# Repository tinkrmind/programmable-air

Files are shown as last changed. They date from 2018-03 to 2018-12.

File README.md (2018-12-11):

## NOTE: Development of Programmable-Air has moved to [Programmable-Air Org repo](https://github.com/programmable-air). This repo is maintained for the sake of completeness but is no longer actively maintained. Please use [Programmable-Air Org repo](https://github.com/programmable-air) for code and reference material.

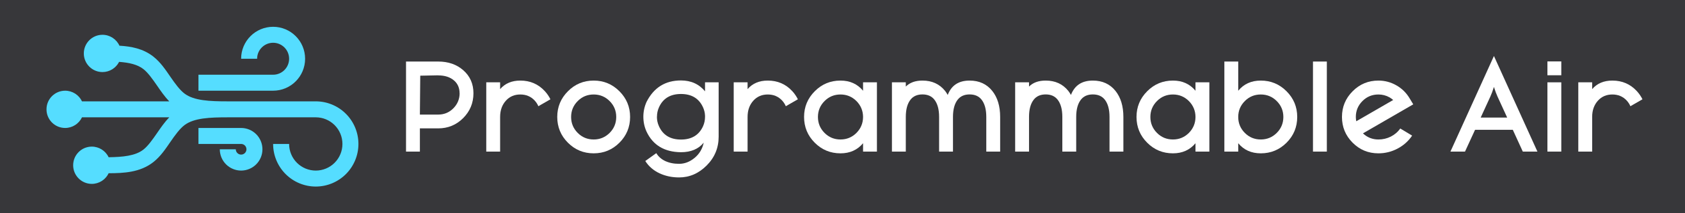
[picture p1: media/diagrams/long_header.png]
Header


## Buzz

* [Hackaday mention!](https://hackaday.com/2018/05/24/programmable-air-makes-robotics-a-breeze/)
* [Hackster mention!!](https://blog.hackster.io/programmable-air-is-an-arduino-based-air-pump-for-your-soft-robotics-projects-9945c6ed96aa)
* [Maker Faire](https://makerfaire.com/maker/entry/67747/)

## Elevator Pitch

quad-chart (https://docs.google.com/presentation/d/1pUnGk4v_wuCpisjBpNWZSJUyDwAFb4v1xceV4rX-Uv4/edit?usp=sharing)

### [Slideshow](https://docs.google.com/presentation/d/1pUnGk4v_wuCpisjBpNWZSJUyDwAFb4v1xceV4rX-Uv4/edit?usp=sharing)

I started out making in earnest at IISc where I saw researchers being exploited by hardware manufacturers. Sub-par equipment is often lauded as the best solution only because it's the only solution. As a result I worked directly with researchers making equipment for measuring elephant height, insect wing- beat frequency, underwater gates for fishes.. I see the same issue with soft robotics today.

The field of inflatable robotics is still in its infancy. So there are a lot of low hanging fruit up for grabs. As such, the more people involved in active experimentation, the faster the field will mature.

Working with inflatables involves a lot of prototyping as a part of the design process. To do any repeatable experiments with inflatables, a controllable air source is required.

I feel there isn't any affordable and easy to use programmable air source available for makers right now. This is a barrier to entry. Programmable Air is my attempt to create a bottom of the line air source that is cheaper and easier to use than anything available right now. The market is strapped for cash makers and schools.

### What can you use it for?

#### Vacuum

###### [* Electronic component pick and place.](https://vimeo.com/268358924)

SMD component pick and place (https://vimeo.com/268358924)

###### [* Universal vacuum based gripper.](https://vimeo.com/268358891)

Universal vacuum based gripper (https://vimeo.com/268358891)

#### Inflatable

###### [* Crazy soft robots]()

###### [* Balloons!](https://vimeo.com/268358970)

Balloons! (https://vimeo.com/268358970)

##### [* Small air brush?](https://vimeo.com/268163619)

Doesn't really work. You can get it to work if the air brush is pointing down and mars is on retrograde :P Check out the failed video below. Maybe it'll give you an idea for how you can improve on it.

Air-Brush (https://vimeo.com/268163619)

 Most airbrushes seem to require around 10L/min air flow rate and the current pump can only deliver 1-2L/min. This small one just barely works with the pumps.

#### Pressure sensor

##### [* Large Impact Sensors]((https://vimeo.com/268358944)

Irregular impact sensors (https://vimeo.com/268358944)

Any closed inflated object can be used as an impact sensor when connected to the air pressure sensor e.g. a large flexible tube with one end closed off and another connected to the pressure sensor. When the tube is pressed a pressure spike is recorded by the sensor. This tube can be looped around a bumper car for example to act as an impact sensor.

##### [Exhalation](https://vimeo.com/268359027)

Exhalation (https://vimeo.com/268359027)

Controlling the air pressure inside a closed chamber allows a soft robot place in the chamber to behave as if it is being controlled without any tubes connected to  it. This facilitates easy prototyping and some funky art pieces. Inspired from [Exhalation](http://escapepod.org/2009/04/10/ep194-exhalation/) by Ted Chiang.

### What's wrong with the current solutions?

#### Pneuduino: [link](http://pneuduino.org/)

Not available for purchase. Potentially fallen out of development(last commit on github was about two years and the primary engineer has graduated out of the program.)

#### Fluidic control system: [link](https://softroboticstoolkit.com/book/control-board)

Truly designed by researchers for reserchers. Ugly. Complicated to setup. Needlessly expensive. [BOM](https://softroboticstoolkit.com/book/controlboard-bom)

Methods of potentially reducing cost:

- __Cheaper pump__: The [current pump](http://ph.parker.com/us/12051/en/btc-iis-and-ttc-iis-miniature-diaphragm-pump) at ~288$ is overpriced if not necessarily overspec'ed. I'm confident a replacement would be available for one tenth the cost.
- __Cheaper valves__: High switching rate is not necessary for most applications. The current valves cost ~175$. An acceptable replacement would be [this](https://www.elecrow.com/dc12v-four-way-valve-independent-control-solenoid-valve.html) at ~10$. Since pressure is controlled by PWM of the valves, this may lead to some issues if these actuators can't be driven fast enough. Some slack can be made up for by adding a "capacitor" after the valve. But, if the actuation time is of the order of hundreds of milliseconds, I may need a different approach. One such approach can be servo driven drip knobs. Another approach could be a linear actuator driving a plate covering a slit
- __Get rid of the power boards__: There's no need for a 24V in which then gets converted to 12V and 5V on board. It adds bulk and points of failure. Separate 12V and 5V wall warts will be much more reliable and cheaper. Cost saving ~20$
- Get rid of mosfets: A ULN2803 would be just as well suited to the task at a fraction of the price. It would also be much more reliable against electrostatic shock.
- __Cheaper air pressure sensors__: The same vendor makes [pressure sensors](https://www.digikey.com/product-detail/en/honeywell-sensing-and-productivity-solutions/NBPLANN100PAUNV/480-5540-ND/3475899) at a forth the price, which only need minimal external circuit to become nearly as accurate. This would add complexity to the first design of the build but bulm manufacture would benefit from the cost saving.
- __Cheaper arduino alternative__: An arduino mega is overkill for this. Any atmega324 based boards is sufficient

The __weakest link__ in this setup however is the __mess of jumper cable__ connections. There is no justifiable reason for a beginners kit to be this complicated to setup especially when the cost can be reduced simultaneously by making the setup into a PCB.

### Let's start making!

pressures

The common pressures are of the range -0.5 atm to 2.5 atm. Ideally we'd want to work in this entire range. Ideally, the pressure profile would be editable over a web interface, without any software/driver installation.

#### Learning basic fluid mechanics and the lingo of the field

Choosing a pressure sensor is tough! There's far too many choices and every datasheet seems to have come from a different universe. Who uses hectoPascals?! Here's some bare minimum info you need before searching for sensors:

-  [Difference between absolute, guage and differential sensors](https://www.first-sensor.com/en/products/pressure-sensors/pressure-sensors-and-transmitters/pressure-types.html)
- [DigiKey sensor guide](https://www.digikey.com/en/resources/sensors/pressure-sensors)
- [Basic of fluid physics](http://www.pneumaticsonline.com/BasicTraining/default.htm)

### Minimum Viable Product

The problem to be solved here is reducing cost without compromising on function. To reduce cost, component specifications have to be matched. The max pressure deliverable by the motor should be close to the pressure limits of the sensor. Given dozens of choices for sensors, motors and valves this is not an easy exercise. Especially, when we're aiming at a moving target specification.

To make life easier, I decided to go for following minimum specifications
* -0.5 atm to +0.5 atm pressure range,
* two air channels
* 2 Liter/min flow rate
* Able to inflate and deflate a 6 inch balloon in under 30 seconds
* Five minute setup time
* Cross platform compatability(Win, Mac, Linux)
* Cost under 100$/set for a production run of 5 sets

### Evaluating off the shelf components

|Item|Inner Dia Eqv|Voltage|Link|Cost per item|Remarks|
|---|---|---|---|---|---|
|Similk aquarium +pump|3/16"|6V|[Amazon](https://www.amazon.com/gp/product/B071FC3C9L/ref=ox_sc_act_title_3?smid=A30FBXYHCPC2G9&psc=1)|4$||
|DIminus aquarium +pump|3/16"|6V|[Amazon](https://www.amazon.com/gp/product/B071GNFHGX/ref=ox_sc_act_title_1?smid=A1KXN55BWHRB5I&psc=1)|4.5$||
|Medical -pump|3/16"|12V|[Amazon](https://www.amazon.com/gp/product/B01MR3JZZF/ref=ox_sc_act_title_4?smid=A3BG62S1F23IH5&psc=1)|9$||
|Square Medical -pump|3/16"|12V|[Amazon](https://www.amazon.com/gp/product/B071GNFHGX/ref=ox_sc_act_title_1?smid=A1KXN55BWHRB5I&psc=1)|11$|Low stock|
|Ohaha tube connectors|3/16"|N/A|[Amazon](https://www.amazon.com/gp/product/B06XHX1KWL/ref=ox_sc_act_title_1?smid=A1665Y00LA4JOM&psc=1)|8$/set of hundred connectors||
|Aquarium -pump|3/16"|5-12V|[Amazon](https://www.amazon.com/Electric-Self-Priming-Suction-Aluminum-Diaphragm/dp/B0786CX98Q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)|10$||
|Pink-day -pump|3/16"|12V|[Amazon](https://www.amazon.com/Pink-day-Electric-Motor-Vacuum-Booster/dp/B076VLXHYB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)|5$|Slow shipping|
|Woolf -pump|3/16"|3-6V|[Amazon](https://www.amazon.com/3V-6V-Motor-Vacuum-Aquarium-Oxygen/dp/B074PPV6QH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)|4$|Slow Shipping|
|Valve 2way|3mm|5V|[Amazon](https://www.amazon.com/gp/product/B00JR3ZQSC/ref=od_aui_detailpages00?ie=UTF8&psc=1)|7.5$||
|Omron +-pressure sensor|3mm|Wheatstone|[DigiKey](https://www.digikey.com/product-detail/en/omron-electronics-inc-emc-div/2SMPP03/Z3639-ND/3671590)|8$|Needs HX711+LM10CN or [INA125](https://learn.adafruit.com/smart-cocktail-shaker/hardware) to work with arduino|
|3 way valve|3/16"|12V|[Elecrow](https://www.elecrow.com/electric-2-position-3-way-12v-micro-solenoid-valve-for-gas.html)|2.5$||
|2 way valve|3/16"|12V|[MPJA](http://www.mpja.com/Solenoid-Valve-Normally-Closed-12VDC-Used/productinfo/33957+HD), [Manufacturer](https://translate.google.com/translate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), [SkyCraft](https://www.skycraftsurplus.com/12vdcpneumaticsolenoidvalve-1.aspx)|2.95$|Reused components. Not scalable.|
|2 way valve |3/16"|12V|[Alibaba](https://jmakervalve.en.alibaba.com/product/60692195756-805059697/JMKV20_BB12A1_2_way_12v_dc_water_solenoid_valve_for_high_end_medical_equipment.html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)|

### Choice of pressure sensor: [2SMPP03](https://www.digikey.com/product-detail/en/omron-electronics-inc-emc-div/2SMPP03/Z3639-ND/3671590)

It's easy for the pressure sensor to be the most expensive piece in the kit. Since one pressure sensor is required for every pneumatic channel, the cost scales linearly with number of channels. Pressure sensors that work in <-0.5 atm to >+0.5 atm range are relatively expensive since few large industries demand such a sensor. The cheapest such sensor I could find is [2SMPP03](https://www.digikey.com/product-detail/en/omron-electronics-inc-emc-div/2SMPP03/Z3639-ND/3671590) by Omron electronics. It is priced at <7$/per unit for 5 units and while it needs additional circuitry to work, the effort is well worth it. The cheapest sensor that works standalone is at least 30$/per unit at 5 units. So I have designed the rest of the system around this sensor.

### v0.1 PCB design

Used Aiyima pumps and an Arduino Nano on master board. The slave board has pressure sensor and three two way valves. Upto four slave boards can attach to a single master board, as shown in mock-up below.

Mock-up of master and slave board positions

#### Learnings from design and manufacture:

The rated current for DC motors can differ highly from the actual current consumed. While the motors are rated at 350mA, a 0.8A transistor blew up while trying to supply enough current to it. This could be because of high stall/startup current. v0.11 will have TIP120 or FET rated to at least 2A. The valves are rated at 0.11A so, using a 2222 transistor seems like a safe bet because they can handle peak currents of up to 0.8A(a 7x margin). Because these are much cheaper than TIP120, it makes sense to use them.

As a result of design oversight, the was no 5V power connection from master to slave board. While 12V input to slave board can be converted to a clean 5V with a relatively cheap regulator, v0.11 will have power connections for 5V as well. Added filter capacitors to all power rails in v0.11.

I manufactured the PCBs in an OtherMill CNC. It is the fastest way I have found to do small run prototypes. Designing for OtherMill manufacture is a completely different game than designing for production from a PCB fab house. Particularly, OtherMill PCBs are constrained to maximum two layers and vias are not plated. Also the tolerances have to be relaxed to allow for easier production. All in all this means you have to be a lot smarter, using minimum number of vias and distributing your components further out.

### Project Update: April 28th

I was finally able to fix the issue with the pressure sensor. I'm using a LM10CN precision opAmp to supply 100uA to the 2SMPP-03 pressure sensor. This results in a 40mV span voltage through the Wheatstone bridge in the sensor, which is read through the HX711 24 bit ADC. While HX711 has the ability to excite the sensor directly, I have not been successful in using this because the IC is poorly documented. LM10CN adds 2.5$ to each pressure sensor unit and complicates the circuit, but the cost savings are still worth the hassle.

I'm looking into using an instrumentation amplifier like INA125 instead of LM10CN+HX711. The cheapest instrumentation amp I could find is 7$, a hefty 3$ more than the HX711+LM10CN setup. Multiply by three/four sensors per kit and that's 10$. not sure if math makes sense. Note that the resolution of data gathered does not matter for this decision(an instrumentation amp would use the Arduino's 10bit ADC vs the 24 bit ADC on HX711), because the data will be corrupted with enough noise that anything above 8 bit resolution should not matter.

I also decided to redesign the boards to be less than 100x50mm in size so that they can be easily manufactured in small batch runs from PCB manufacturers. 100x100mm panel size seems to be a universal cutoff for price variation(at least when it comes to hobby type boards). I utilized this avenue to add M3 mounting holes and standardize the berg stick connectors better.

After using the board for a bit, I realized that most applications call for less than three air channels and I was using the fourth channel almost exclusively for IO. So I put two buttons and a few neopixels on the master board using up the pins from the fourth channel. Now the slave boards can only dock to the bottom or sides of the master boards, and not to the top. The top has easily accessible power connection, USB, buttons and neopixels. I also added LEDs to indicate the state of the pumps and valves. And I put the pumps on analogWrite pins for the atmega328. This will allow me to easily control the pumping speed.

As an additional fun challenge, I decided to only use curved angles in the PCB traces. I think the PCBs came out looking rather sharp. On the practical side, since I manufacture PCBs with a CNC the lack of sharp corners translates to quieter, less jerky operation while manufacturing.

### Working with Balloons - Case for flow meter

Programmable Air gets feedback from a pressure sensor. This is because I was following an unwritten intuition that the pressure inside an inflatable is proportional to the volume of air pumped in. Boy! is that intuition wrong! For rubber inflatables like latex balloons or thin walled silicone the pressure initially increases with the air flow but then starts decreasing. The balloon is more of a flow driven device than a pressure driven device. To control something like this a flow meter makes much more sense. The initial case against a flow meter was because of leaks. It makes sense to have a flow sensor to use in conjunction with a pressure sensor as well. I'm on the lookout for a cheap flow sensor.

**Result**: Flow sensors are too expensive! Like 80$ for a [cheap one](https://www.digikey.com/product-detail/en/honeywell-sensing-and-productivity-solutions/AWM1100V/AWM1100V-ND/2552655). Not even gonna think about using it for a while.

### Changes I'd like to work on:
* LittleBits or mCookie like magnetic snap connectors instead of dupont sticks. Failing that, just plain better connections.. dupont connectors aren't meant for this kind of mechanical strains. Maybe old school RS232 or serial type stuff?
* Manage power to motors and solenoids better. e.g. Arduino USB should not power the motors when no Vin is provided.
* Make pneumatic connections via simple snapping as well. Individually connecting cables is so 2000's :P
* Simpler custom connectors to make pneumatic connections. Aquarium type connectors are very restrictive.
* Cheap 3mm to 3/16th converter

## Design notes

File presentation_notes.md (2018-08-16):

# Programmable Air

I started making in earnest when I was at Indian Institute of Science. I found my niche there as the engineering advisor for the Center of Ecological Sciences. I'd often see sub par equipment being lauded as the best solution simply because it was the only solution. In my battle against overpriced equipment I made a height sensor for elephants, a wind tunnel, sensor for measuring insect wing beat frequency amongst other things.

So when I looked at the Harvard soft robotics kit, I was in familiar terrain. The kit is obviously designed by researchers for researchers. It is expensive, ugly and bulky. Kinda the worst of all worlds. Programmable Air is a project born out of pure hatred.

### The journey
* Reading up on pneumatics
  - Guage pressure, absolute pressure, differential pressure
  - Who uses hectopascals and dLpms?
* Dozens of hours searching for Components
  - dozens of websites
  - hundreds of Components
  - figuring out components that are not only compatible electrically and have the same pressure range and flow rate but also use the same size connectors
* Ordering Components
  - the bane of every fabrication project - the wait-time
* Evaluating components
  - evaluated five motors
  - few different valve types
* Designing PCBs
  - Eagle vs KiCAD
  - obscure components had to design the component libraries
* Manufacturing PCBs
  - Curves! - annoying to get right, but a treat for eyes and ears
* Getting it wrong
  - Redesign, remake
  - *Throw PCBs* It's safe to say that I've made a few mistakes

### How does Programmable Air work?
* Components:
  - Pump board
    - Arduino nano
    - Two vacuum/air pressure pumps
    - Connections to accommodate up to three valve boards
    - Some LEDs and buttons
  - Valve board
    - +- 0.5 atm pressure sensor
    - Three normally closed valves

* Air channels for full control of pressure-

### Limitations
* Pressure range -0.5atm to +0.5 atm
  - Lots of interesting things happen outside this range
    - Caveat: higher pressure range will need better, costlier connectors
* Flow rate 2lpm
  - Not suitable for fast applications
    - Caveat: faster pumps and valves will increase size and power requirement

### Experts:
* Ben- look at similar industries -aquariums,
* Eric- get cheap second hand industrial stuff
* Tom- make a kick ass tutorial
* Sebastian- Don't reinvent the software, make a great library
* Yuli- Give full control of the air channel

### Special thanks for lending equipment
* Kemi
* Keerthana and Azalea
* Sebastian
* Lola

### Mistakes made:

* Cheaping-out on the ADC for pressure sensor - taring is annoying. Multi sensor support is still iffy
  - Solution: Move to an instrumentation amp with constant current driver. Haven't found one yet.
* Cheaping-out on the air valves. They leak at high pressure and have high resistance to flow.
  - Solution: Evaluate the more valves. Haven't found a replacement yet.

### Presentation Demos:

* Universal jamming gripper
* SMD pick and place
* Rube Goldberg
* Irregular impact sensor
  - leave room for serendipity
* Balloon pressure
* Exhalation

### What else can you make?
* Bubbles!
* Wind instruments!

### Timeline:
* 1.5 min- inspiration & current solutions
* 0.5 min- common pressure ranges
* 1 min-

### What I want from you!
* How do you see programmable air?
  - (a) A kit like makey makey?
  - (b) Little bits or grove modules
  - (c) Standalone Arduino compatible modules
  - (d) ?

Audience: ITP first year student

### BOM

For production of 10 units.

|Item|Cost|
|---|---|
|Pumps|8$|
|Valves|9$|
|Pressure sensor|12$|
|Arduino Nano| 4$|
|TIP120|2$|
|Passives| 2$|
|LEDs|1$|
|Electrical connectors|1$|
|PCBs|2$|
|Tubes|2$|
|Pneumatic connectors|2$|
|Power supply|3$|
|USB Cable|2$|
|Total|50$|

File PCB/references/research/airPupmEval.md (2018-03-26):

I evaluated readily available pumps on Amazon.com, giving preference to 12V pumps over 6V/24V pumps so that there will be no need for voltage regulation. The desired pump characteristics were:

- 12V operation
- Pressure > 30PSI(~2bar/1500mm Hg)
- Cost < 25$
- Compact size (~ 3"x3"x3" or less)

Some of the pumps evaluated and reasons for failure:

- [Saim DC 12V](https://www.amazon.com/Saim-Motor-Aquarium-Oxygen-Circulate/dp/B0716V496V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) Cheap, compact, 12V but only 350mm HG Pressure
- [Keurig Replacement Mini Air Pump](https://www.amazon.com/Keurig-Replacement-Mini-U-S-SOLID/dp/B01BFNEVEQ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) Compact, 12V but only 350mm HG Pressure
- [Powerful DC 12V air pump ](https://www.amazon.com/dp/B01LRWOFHS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) ~5PSI

Multiple other candidates were also evaluated but the general trend was lack of pressure. Given that large tyre inflator type pumps are relatively low cost(<40$) it might be worth going the route of pneuduino and use a large **offboard pump** instead. This will **reduce portability significantly.**

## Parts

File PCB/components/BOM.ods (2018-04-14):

Item | Description | Cost | Manufacturer Link | Purchase Link
CJV23 | Solenoid fluid valve | 2.95$ | http://www.conjoin.com.cn/products.php?l=5 | http://www.mpja.com/Solenoid-Valve-Normally-Closed-12VDC-Used/productinfo/33957+HD | https://www.aliexpress.com/item/Mini-Micro-DC12V-Electric-Solenoid-Valve-Gas-Air-Water-Normally-Closed-OD-5mm-Plastic/32736292994.html | https://www.aliexpress.com/item/DC-12V-Normally-Closed-Type-Electronic-Control-Solenoid-Discouraged-Air-Valve-328-313/32856372733.html
2SMPP03 | Air pressure sensor | 7$ |  | https://www.digikey.com/product-detail/en/omron-electronics-inc-emc-div/2SMPP03/Z3639-ND/3671590
Aiyima pump |  |  | https://www.amazon.com/Aiyima-Vacuum-Medical-Negative-Pressure/dp/B01IHPZ1WG | https://www.amazon.com/Aiyima-Vacuum-Medical-Negative-Pressure/dp/B01IHPZ1WG

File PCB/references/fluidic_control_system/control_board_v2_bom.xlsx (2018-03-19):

DESCRIPTION | QUANTITY | UNIT COST | TOTAL COST | PART NUMBER | SUPPLIER | PURCHASE LINK | SPEC SHEET | NOTES
Pressure source
Miniature Diaphragm Pumps - Air/Gas | 1 | 288 | $288.00 | D737-23-01 | Parker.com | Web Link (http://ph.parker.com/us/12051/en/btc-iis-and-ttc-iis-miniature-diaphragm-pump/d737-23-01) | Web Link (http://ph.parker.com/us/12051/en/btc-iis-and-ttc-iis-miniature-diaphragm-pump/d737-23-01)
Flow control
Manifold, High Flow | 1 | 35.25 | $35.25 | VV3Q12U-04-01N | SMC USA | Web Link (http://www.smcpneumatics.com/VV3Q12U-0401N.html) | Brochure (no spec sheet available) (https://content.smcetech.com/pdf/VQ_3Pt.pdf)
Valve 3-Way, NC, 24DC, High Flow | 4 | 27.2 | $108.80 | VQ110U-5M | SMC USA | Web Link (http://www.smcpneumatics.com/VQ110U-5M.html) | Specs included here (http://www.smcpneumatics.com/VQ110U-5M.html)
Power MOSFETs: 4 Opto-Isolated Power FET Switches (Improved Version) | 1 | 18 | $18.00 | AB-020101 | yourduino | Web Link (http://yourduino.com/sunshop2/index.php?l=product_detail&p=60) | n/a | Used to open and close the valves - can also be used to regulate the pressure using PWM. Alternative is to use a regulator, but you'll need MOSFETs either way
One-touch Fitting, 1/8" Tube, M5 Connection Thread, New Series | 10 | 3.05 | $30.50 | KQ2H01-M5N | SMC USA | Web Link (http://www.smcpneumatics.com/KQ2H01-M5N.html) | Series Catalog (Page 78) (http://www.smcpneumatics.com/pdfs/KQ.pdf) | Connectors for the manifold outlets - 4 needed but sold in packs of 10
Fiting, Male Connector, 1/4" Tube, 1/8" NPT | 10 | 1.1875 | $11.88 | KQ2H07-34NS | SMC USA | Web Link (http://www.smcpneumatics.com/KQ2H07-34NS.html) | Specs included here (http://www.smcpneumatics.com/KQ2H07-34NS.html) | Connector for the manifold inlet - only 1 needed but sold in packs of 10
Pressure SENSOR 100 PSI GAGE 5V | 4 | 44.71 | $178.84 | 480-3306-ND | Digikey | Web Link (http://www.digikey.com/product-search/en?x=5&y=19&lang=en&site=us&KeyWords=480-3306-ND) | Data Sheet (http://sensing.honeywell.com/index.php/ci_id/45330/la_id/1/document/1/re_id/0)
Fitting, Bulkhead Union, 1/8" Tube | 10 | 5.93 | 59.3 | KQ2E01-00N | SMC USA | Web Link (http://www.smcpneumatics.com/KQ2E01-00N.html) | Series Catalog (http://www.smcpneumatics.com/pdfs/KQ.pdf) | Connectors to make attaching different actuators more convenient - Labeled "Outputs" in control board image
Power
Blue 5-25V to 0.5-25V DC Boost-buck Converter 2A Step Up Down Voltage Regulator | 2 | 9.89 | $19.78 | 90637 | Pro DC to DC | Web Link (http://www.prodctodc.com/blue-525v-to-0525v-dc-boostbuck-converter-2a-step-up-down-voltage-regulator-p-432.html) | Specs included here (http://www.prodctodc.com/blue-525v-to-0525v-dc-boostbuck-converter-2a-step-up-down-voltage-regulator-p-432.html) | We need 24V, 12V, and 5V - these chips can be used to take a single input voltage (e.g. 24V) and convert to our requirements. Alternative is to use 3 different power supplies.
CABLE ASSY 5.5X2.1MM Male/Female Jack | 15 | 3.05 | $45.75 | CP-2216-ND | Digikey | Web Link (http://www.digikey.com/product-search/en?x=19&y=18&lang=en&site=us&KeyWords=CP-2216-ND) | Data sheet (http://www.tensility.com/pdffiles/053-0384R.pdf) | To plug in our power supply - if using power supplies instead of above chipes, will need 3 of these
Electronics
Arduino Mega | 1 | 21 | $21.00 | AA-021205 | yourduino | Web Link (http://yourduino.com/sunshop2/index.php?l=product_detail&p=387) | Specs here (http://arduino.cc/en/Main/ArduinoBoardMega2560)
Toggle switch | 6 | 1.75 | $10.50 | B001TJ0ZAG | PartsExpress | Web Link (http://www.amazon.com/SPST-Light-duty-Toggle-Switch/dp/B001TJ0ZAG) | Data sheet, page 272-273 (http://www.masterelectronics.com/datasheet/35-064.aspx?p=11403383)
Potentiometer | 4 | 0.95 | $3.80 | COM-09939 | SparkFun | Web Link (https://www.sparkfun.com/products/9939) | Data Sheet (https://www.sparkfun.com/datasheets/Components/General/R12-0-.pdf)
Breadboard (with jumper wires) | 2 | 13.5 | $27.00 | B004RXKWDQ | microtivity | Web Link (http://www.amazon.com/dp/B004RXKWDQ?tag=microtivity-20&m=A2E0IHQCUI9LTK) | n/a
Optional
Regulator, 24DC, High Flow | 1 | 297.5 | $297.50 | ITV1031-21N2BL4 | SMC USA | Web Link (http://www.smcpneumatics.com/ITV1031-21N2BL4.html) | Series Catalog (http://www.smcpneumatics.com/pdfs/ITV.pdf)
Control board
Colored Sheets Cast Acrylic (6 mm - White) 30x30 cm | 1 | $9.42 | $9.42 | 8505K91 | McMaster | Web Link (http://www.mcmaster.com/) | n/a
Colored Sheets Cast Acrylic (3 mm - Red) 30x30 cm | 2 | $6.74 | $13.48 | 8505K11 | McMaster | Web Link (http://www.mcmaster.com/) | n/a
Not listed
Tubing
Connectors
Screws, nuts, etc.

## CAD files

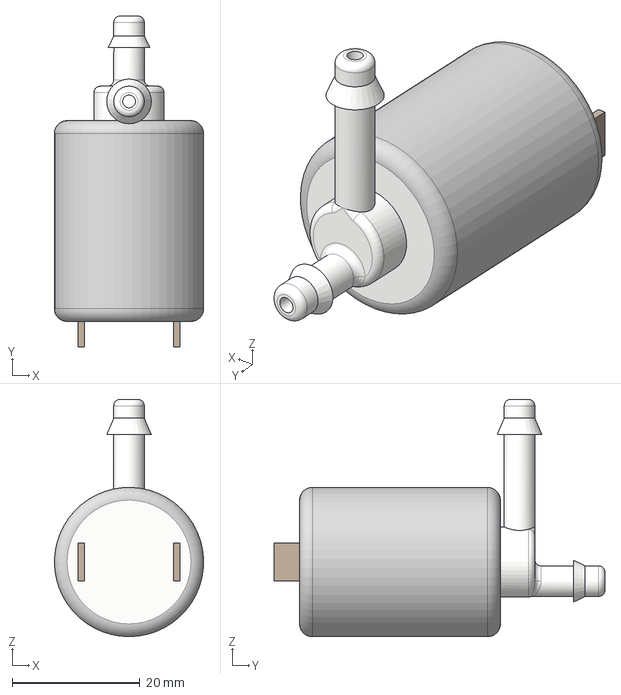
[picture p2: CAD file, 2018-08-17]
CAD/CJV23 v3.step
23.4 x 51.9 x 37.2 mm

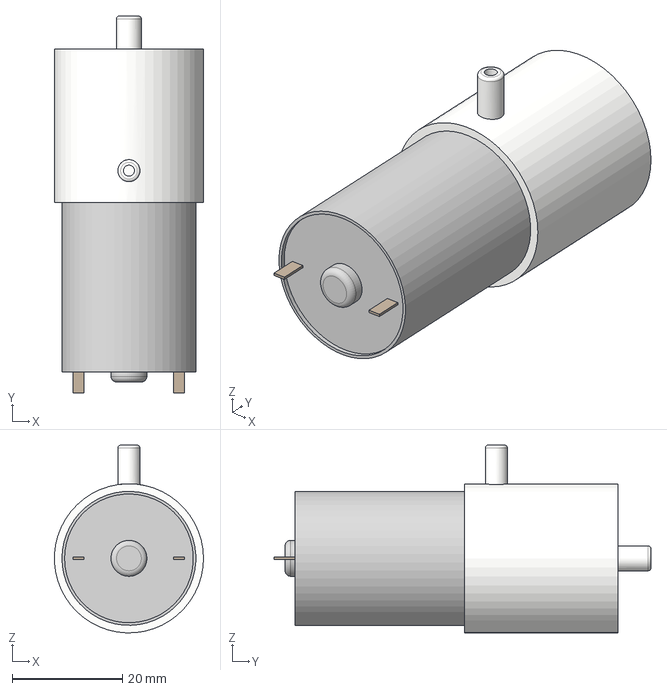
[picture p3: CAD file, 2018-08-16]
PCB/programmable-air-v0.3/Eagle libraries/motor_v3.step
27.0 x 68.2 x 34.0 mm

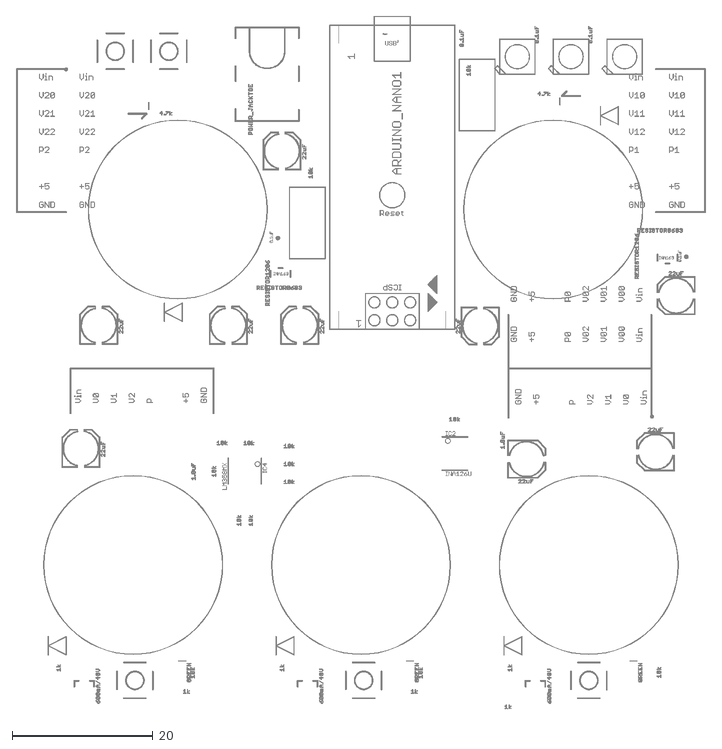
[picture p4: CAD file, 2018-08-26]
PCB/programmable-air-v0.3/master-board plus slave.dxf
98.0 x 98.5

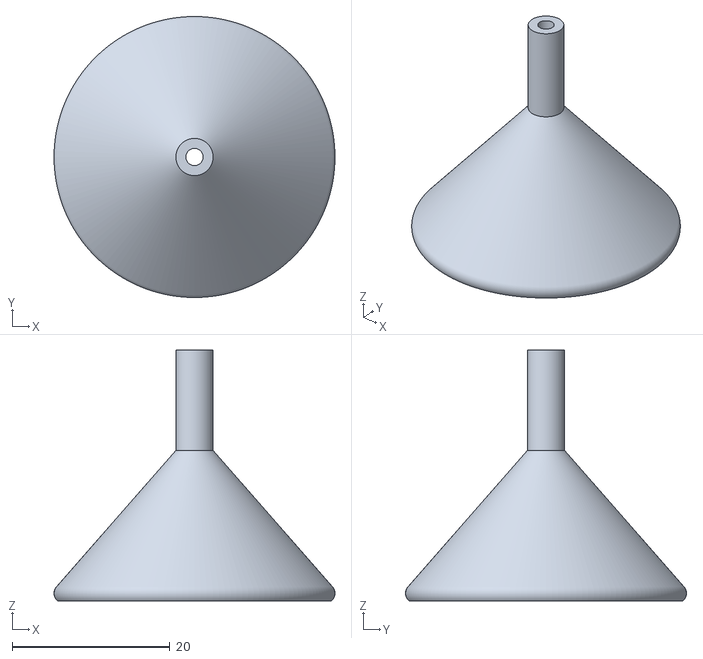
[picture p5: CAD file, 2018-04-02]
PCB/references/funnel.stl
35.6 x 35.6 x 31.8

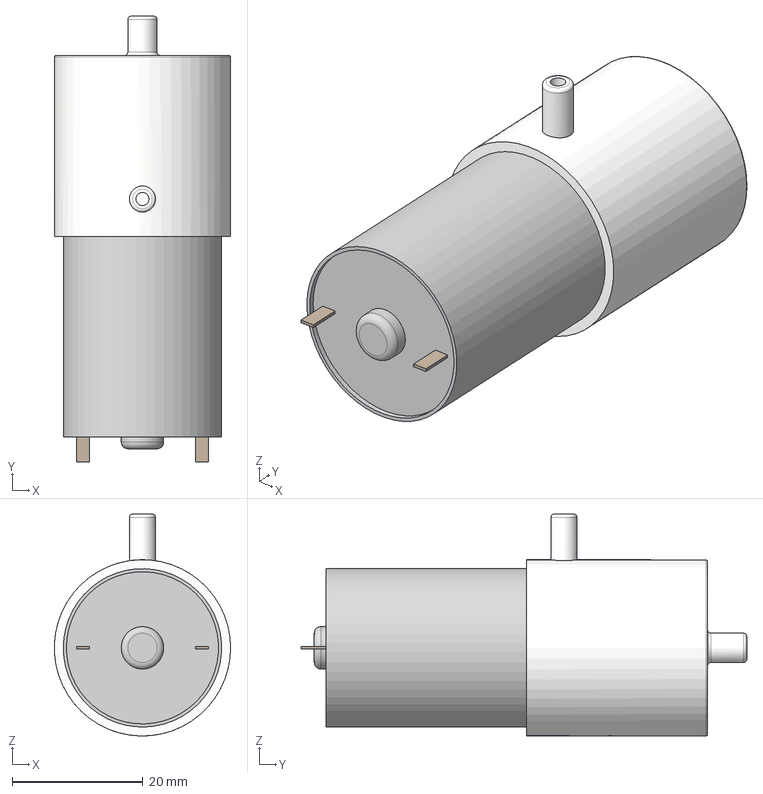
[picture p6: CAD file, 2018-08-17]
CAD/motor v4.step
27.0 x 68.2 x 34.0 mm

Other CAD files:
PCB/programmable-air-v0.3/Eagle libraries/CJV23_v2.f3d

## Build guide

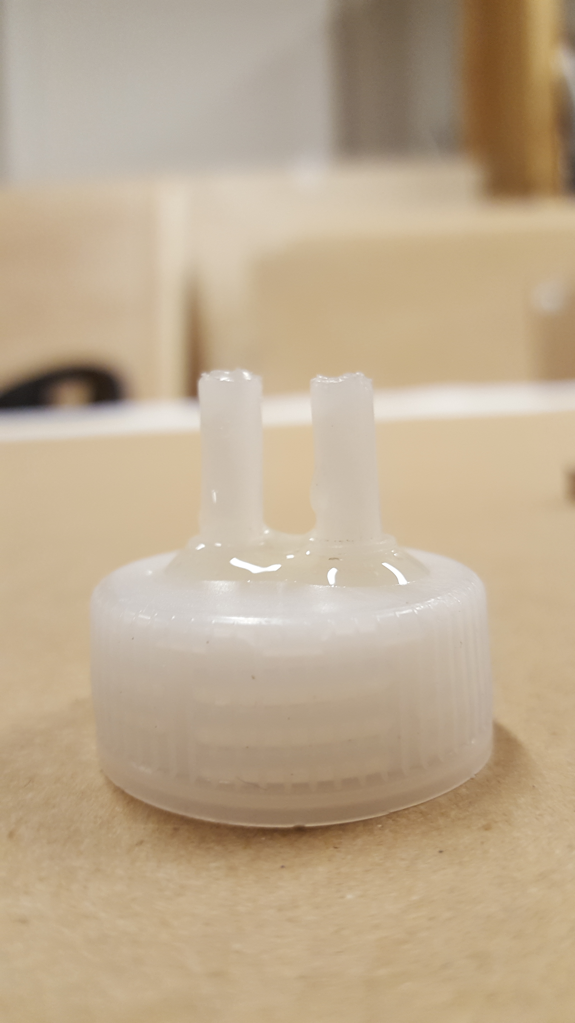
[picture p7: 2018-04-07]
media/build photos/20180407_040647.jpg

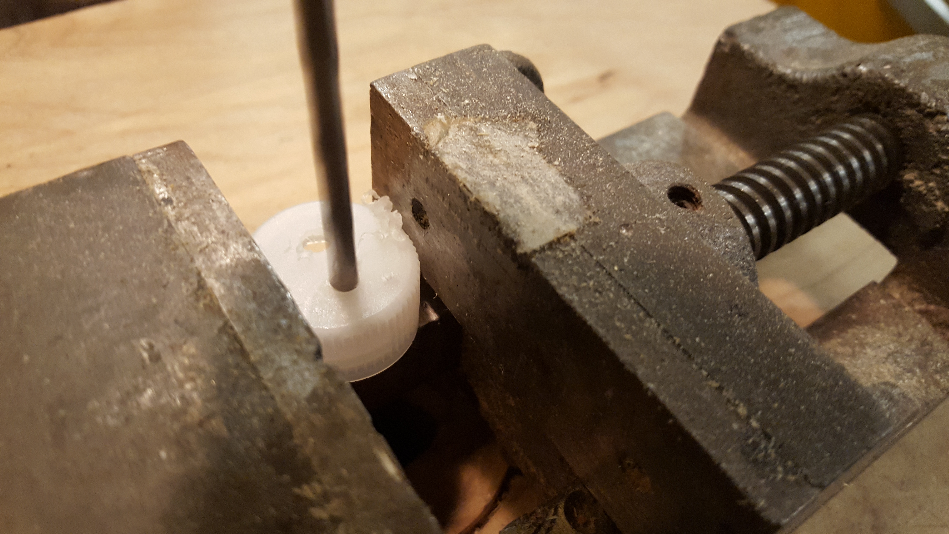
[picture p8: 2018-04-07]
media/build photos/20180407_035953.jpg

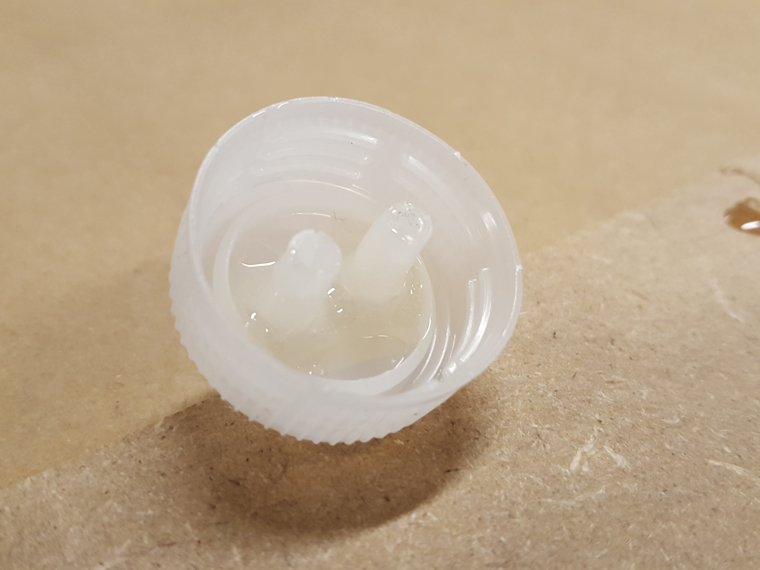
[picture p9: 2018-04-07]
media/build photos/20180407_040732.jpg

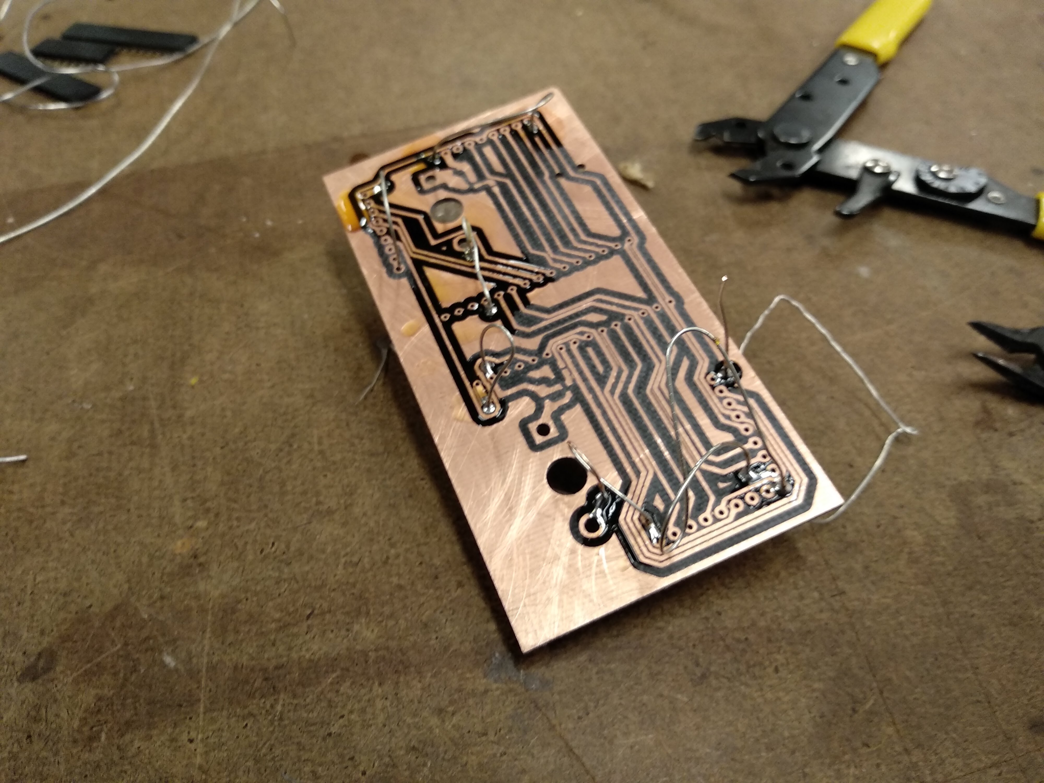
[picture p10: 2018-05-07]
media/build photos/assemble.jpg

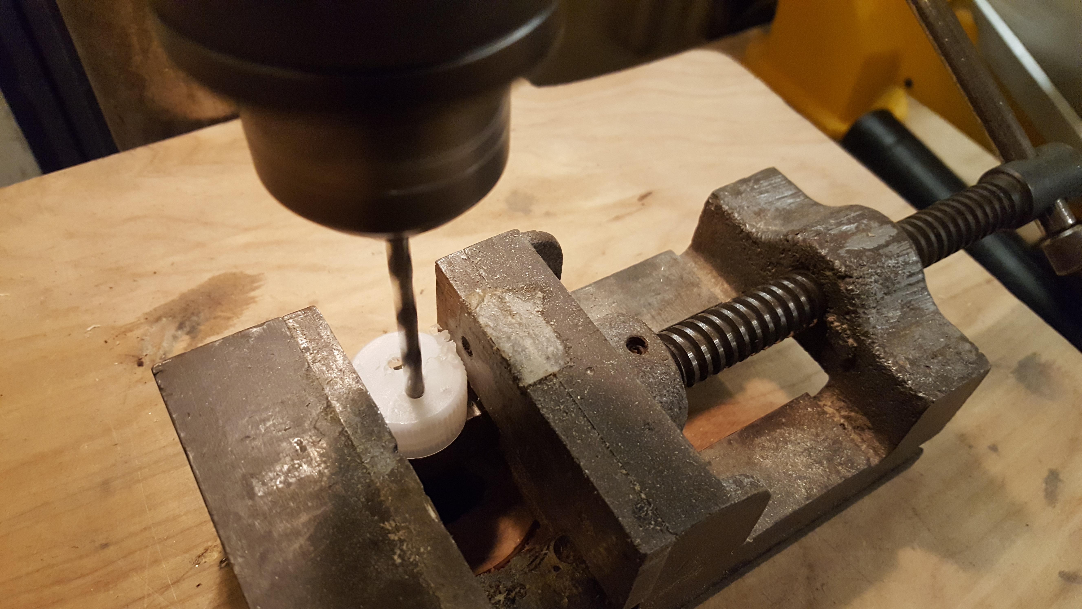
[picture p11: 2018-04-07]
media/build photos/20180407_040002.jpg

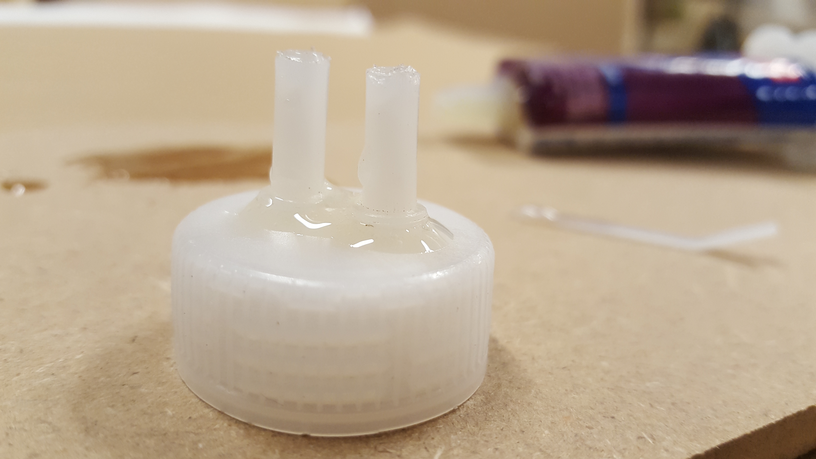
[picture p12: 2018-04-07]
media/build photos/20180407_040628.jpg

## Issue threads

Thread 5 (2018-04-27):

Fix pressure sensor

tinkrmind, 2018-04-27:

tinkrmind, 2018-04-29:
Fixed.

Closed 2018-04-29.

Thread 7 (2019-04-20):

Question about the pump and the gripper

Hoototo, 2019-04-20:
Hi @tinkrmind
I am very interested in your vacuum air project. After seeing the video, I still have some question.
1. The gripper looks very powerful, so how do you make that? Do you fill some material inside?
2. You use 7 different pumps, why? How do you connect the pumps?
3. How much vacuum could you get?
4. How long does it take from work to stability?

tinkrmind, 2019-04-20:
Hi Nick, thanks for the interest. You should know that this repository is only for archival purposes and I'm developing the project at github.com/programmable-air. Here are the answers to your questions:
1- The gripper is filled with coffee grounds.
2- I evaluated seven pumps, but finally settled on using the Pink-day-pump
3- The pump generates about -7.5PSI vacuum
4- Not sure I understand this question. Could you elaborate?

Hoototo, 2019-04-21:
Hi Amitabh
Thanks for your reply soon.
The fourth question is that when the pumps start work and suck the air, how long does it take to pump out all air.

tinkrmind, 2019-04-21:
Ah, it's maybe half a second.

Closed 2019-04-21.

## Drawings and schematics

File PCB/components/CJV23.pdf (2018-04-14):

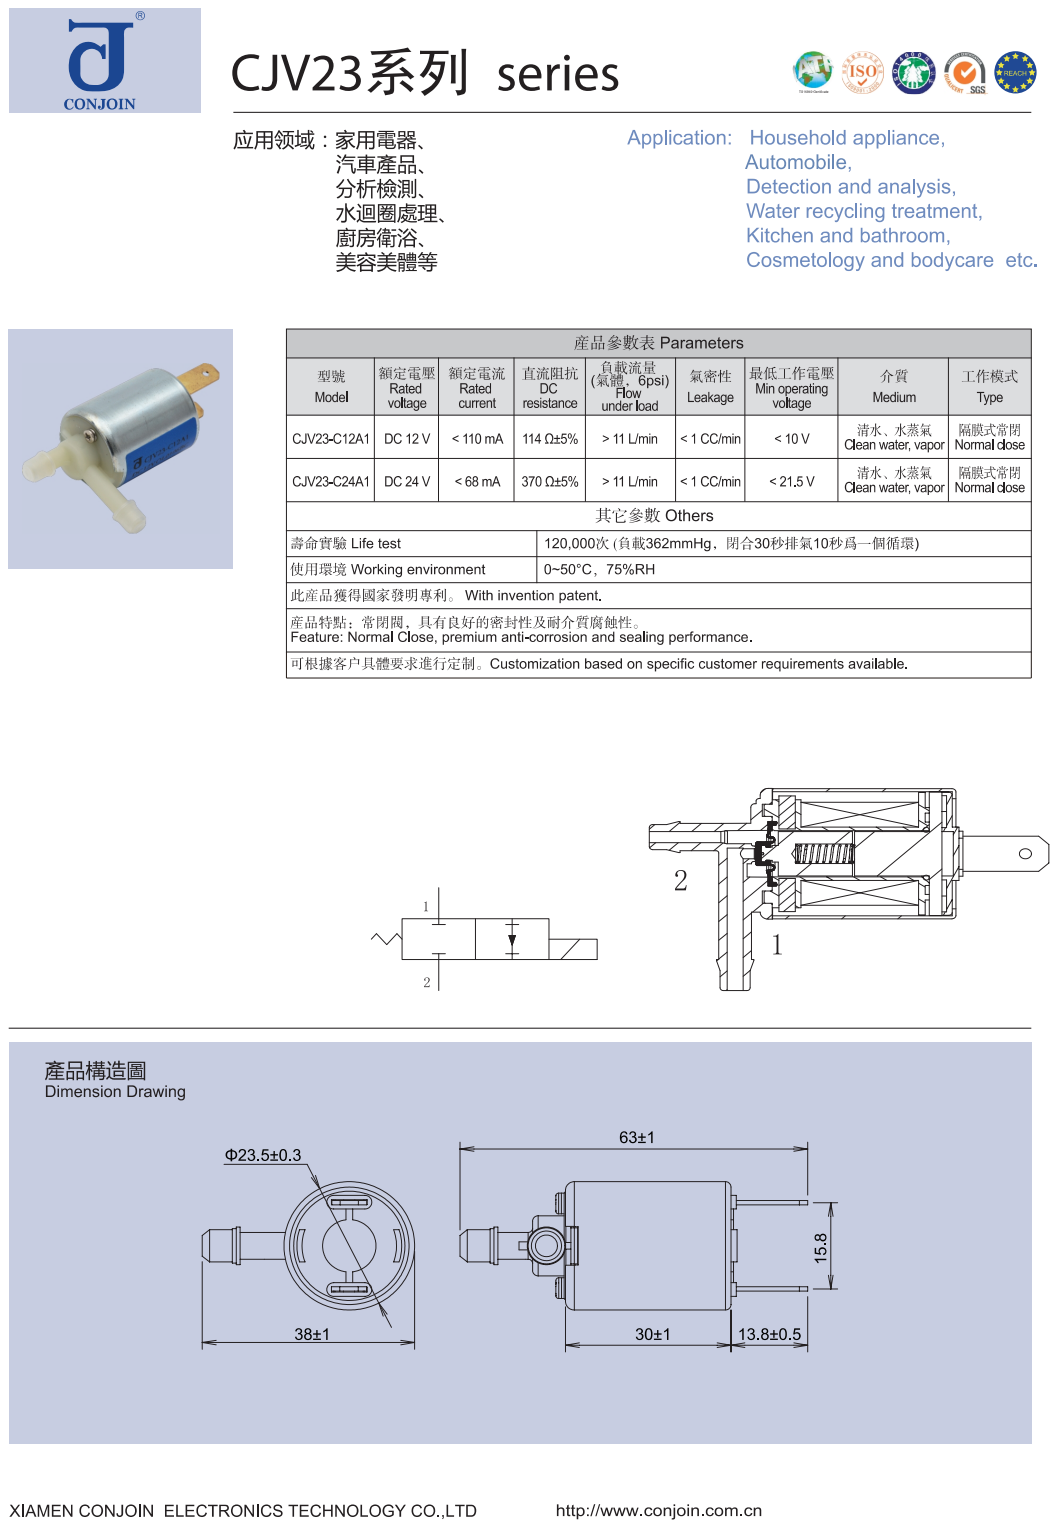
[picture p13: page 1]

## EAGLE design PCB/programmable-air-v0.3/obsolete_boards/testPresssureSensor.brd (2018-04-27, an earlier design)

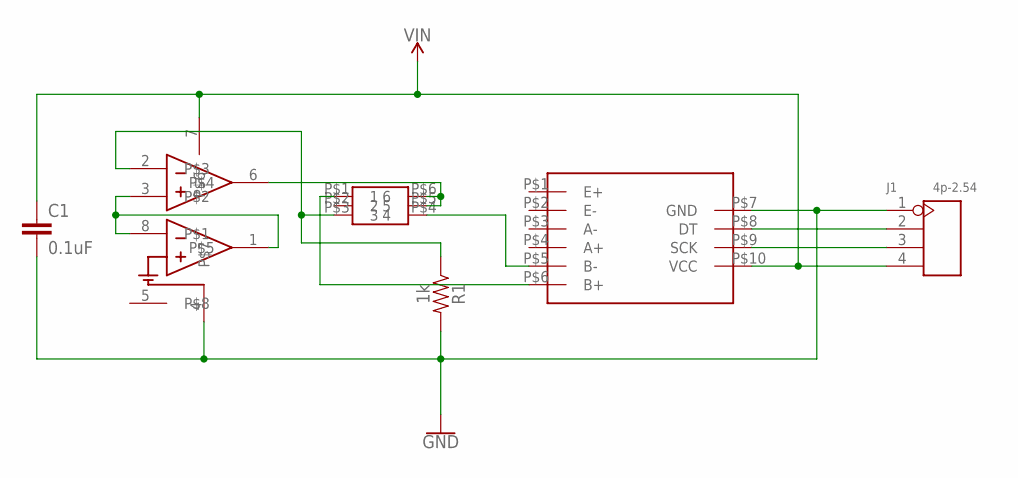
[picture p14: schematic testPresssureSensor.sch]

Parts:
C1: 0.1uF; 0603
J1: 4p-2.54; H4-2.54
R1: 1k; AXIAL-0.3
U$1: 2SMPP-03
U$2: HX711
U$3: LM10CN; DIP8

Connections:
GND: C1.2, J1.1, R1.P$2 (2), U$2.P$7 (GND), U$3.4
unnamed: U$1.P$4 (4), U$2.P$5 (B-)
unnamed: U$3.1, U$3.3, U$3.8
unnamed: U$1.P$5 (5), U$1.P$6 (6), U$3.6
unnamed: R1.P$1 (1), U$1.P$3 (3), U$3.2
unnamed: U$1.P$1 (1), U$2.P$6 (B+)
unnamed: J1.2, U$2.P$8 (DT)
unnamed: J1.3, U$2.P$9 (SCK)
VIN: C1.1, J1.4, U$2.P$10 (VCC), U$3.7

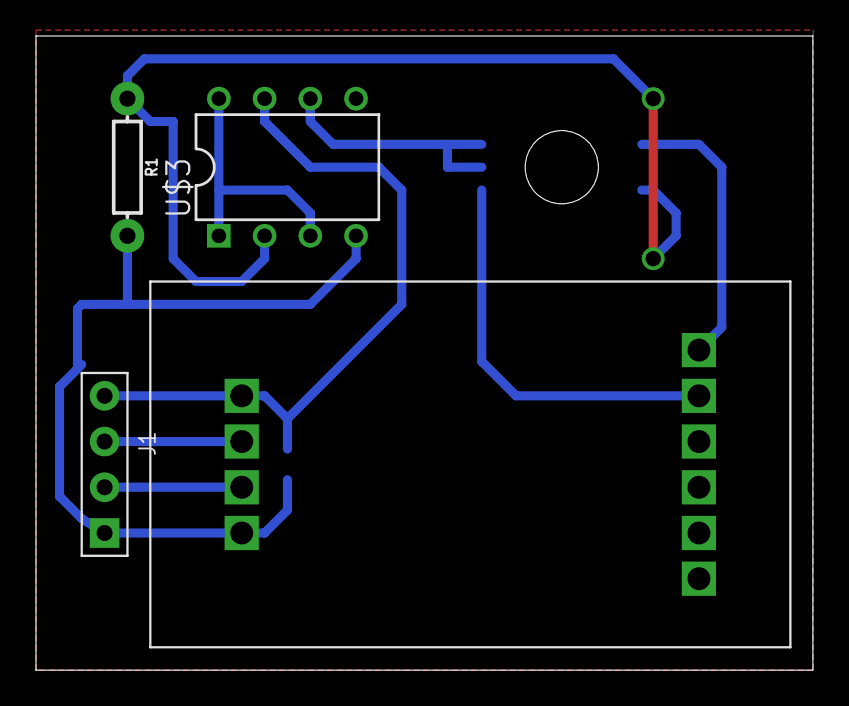
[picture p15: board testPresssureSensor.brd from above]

Board: 2 copper layers, 43.2 x 35.2 mm, 6 parts (1 on the bottom side), 9 nets.

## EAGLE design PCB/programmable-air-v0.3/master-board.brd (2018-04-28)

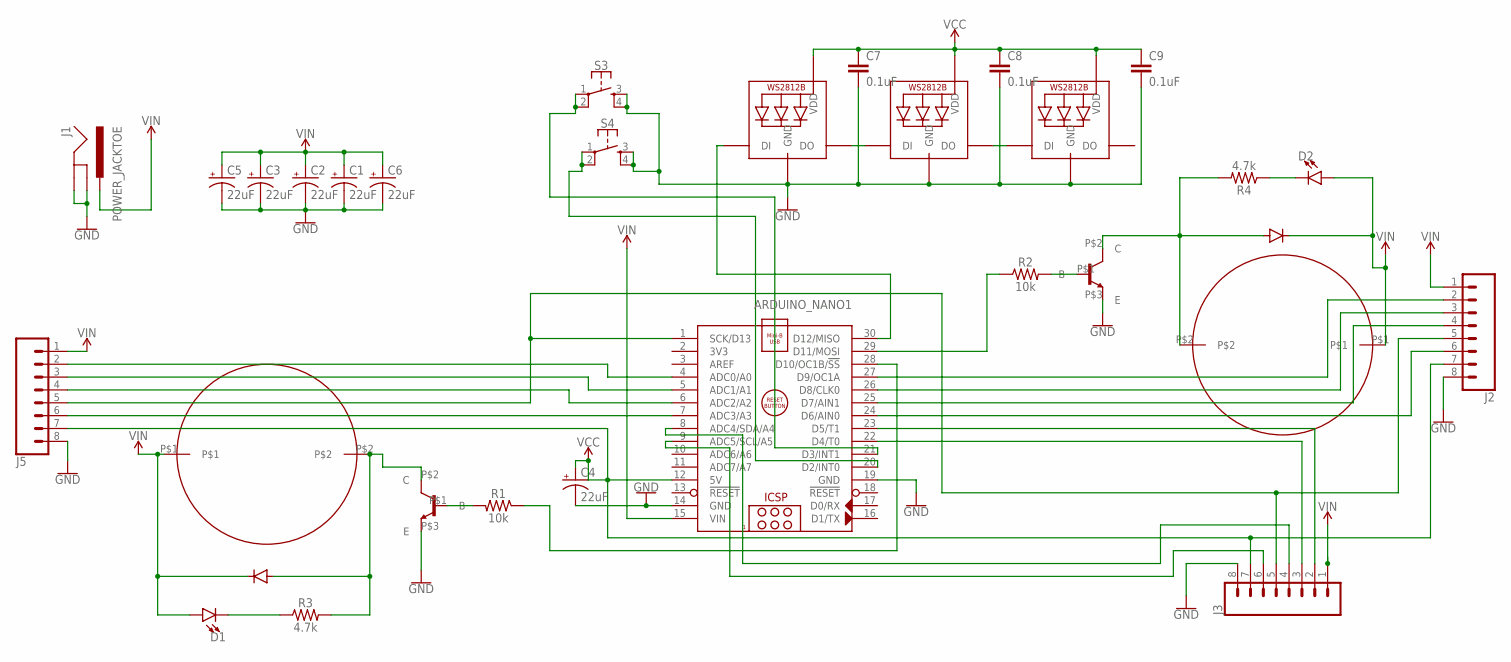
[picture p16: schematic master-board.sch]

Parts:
ARDUINO_NANO1: ARDUINO_NANO
C1, C2, C3, C4, C5, C6: 22uF; PANASONIC_C
C7, C8, C9: 0.1uF; 0603
D1, D2: LED0603; LED-0603
J1: POWER_JACKTOE; POWER_JACK_SMD_OVERPASTE_TOE
J2, J3, J5: CONN_08"; 1X08
LED1, LED2, LED3: WS2812B5050; WS2812B
R1, R2: 10k; 0603
R3, R4: 4.7k; 0603
S3, S4: MOMENTARY-SWITCH-SPST-2-SMD-4.6X2.8MM; TACTILE_SWITCH_SMD_4.6X2.8MM
U$1, U$2: AIYIMA-PUMP-A5F083; A5F083
U$3, U$4: IN4148
U$5, U$6: TIP120-TO220; TO220

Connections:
GND: ARDUINO_NANO1.14 (GND), ARDUINO_NANO1.19 (GND), C1.-, C2.-, C3.-, C4.-, C5.-, C6.-, C7.2, C8.2, C9.2, J1.GND (GNDBREAK), J1.P$4 (GND), J2.8, J3.8, J5.8, LED1.3-GND (GND), LED2.3-GND (GND), LED3.3-GND (GND), S3.3, S3.4, S4.3, S4.4, U$5.P$3 (E), U$6.P$3 (E)
unnamed: ARDUINO_NANO1.29 (D11/MOSI), R2.1
unnamed: R1.2, U$6.P$1 (B)
unnamed: ARDUINO_NANO1.23 (D5/T1), J3.2
unnamed: ARDUINO_NANO1.22 (D4/T0), J3.3
unnamed: R3.2, U$1.P$2, U$3.P$2, U$6.P$2 (C)
unnamed: R4.2, U$2.P$2, U$4.P$2, U$5.P$2 (C)
unnamed: R2.2, U$5.P$1 (B)
unnamed: ARDUINO_NANO1.30 (D12/MISO), LED1.4-DIN (DI)
unnamed: ARDUINO_NANO1.8 (ADC4/SDA/A4), J3.4
unnamed: ARDUINO_NANO1.28 (D10/OC1B/!SS), R1.1
unnamed: ARDUINO_NANO1.5 (ADC1/A1), J5.3
unnamed: D1.C, R3.1
unnamed: ARDUINO_NANO1.1 (SCK/D13), J2.5, J3.5, J5.5
unnamed: ARDUINO_NANO1.7 (ADC3/A3), J5.6
unnamed: ARDUINO_NANO1.9 (ADC5/SCL/A5), J3.6
unnamed: ARDUINO_NANO1.4 (ADC0/A0), J5.2
unnamed: D2.C, R4.1
unnamed: ARDUINO_NANO1.6 (ADC2/A2), J5.4
unnamed: ARDUINO_NANO1.20 (D2/INT0), S4.1, S4.2
unnamed: LED2.2-DOUT (DO), LED3.4-DIN (DI)
unnamed: ARDUINO_NANO1.24 (D6/AIN0), J2.6
unnamed: ARDUINO_NANO1.25 (D7/AIN1), J2.4
unnamed: ARDUINO_NANO1.26 (D8/CLK0), J2.3
unnamed: ARDUINO_NANO1.27 (D9/OC1A), J2.2
unnamed: LED1.2-DOUT (DO), LED2.4-DIN (DI)
unnamed: ARDUINO_NANO1.21 (D3/INT1), S3.1, S3.2
VCC: ARDUINO_NANO1.12 (5V), C4.+, C7.1, C8.1, C9.1, J2.7, J3.7, J5.7, LED1.1-VDD (VDD), LED2.1-VDD (VDD), LED3.1-VDD (VDD)
VIN: ARDUINO_NANO1.15 (VIN), C1.+, C2.+, C3.+, C5.+, C6.+, D1.A, D2.A, J1.VIN0 (PWR), J2.1, J3.1, J5.1, U$1.P$1, U$2.P$1, U$3.P$1, U$4.P$1

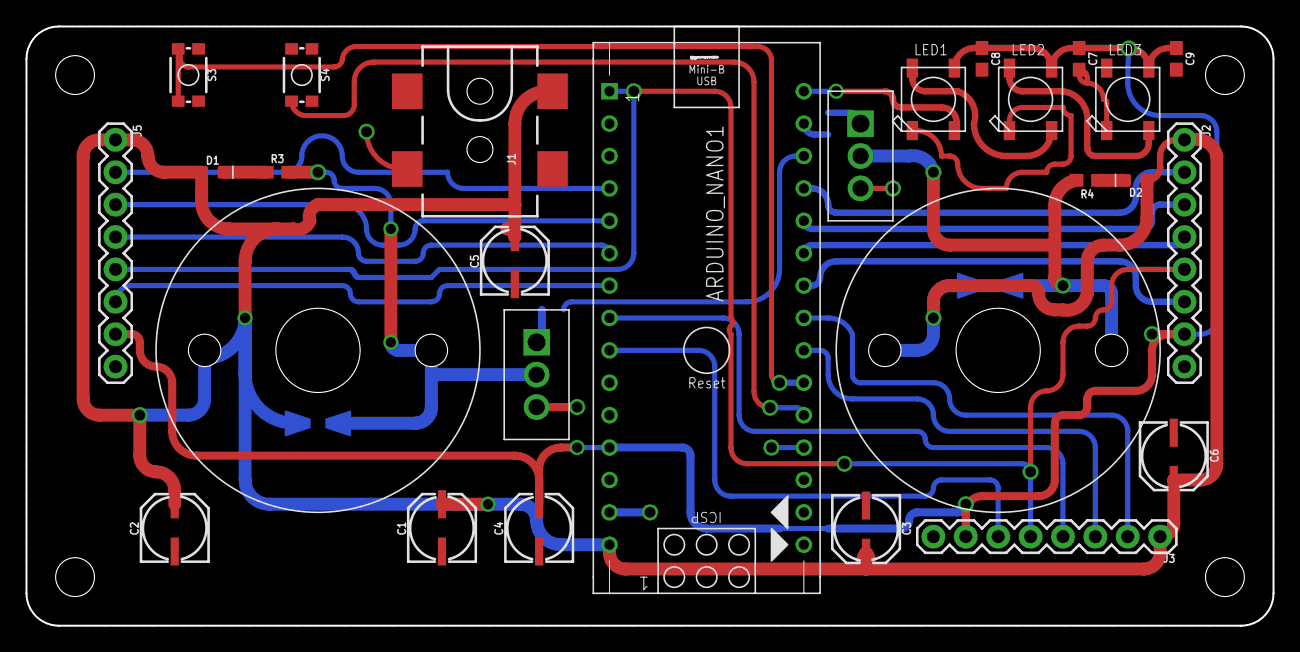
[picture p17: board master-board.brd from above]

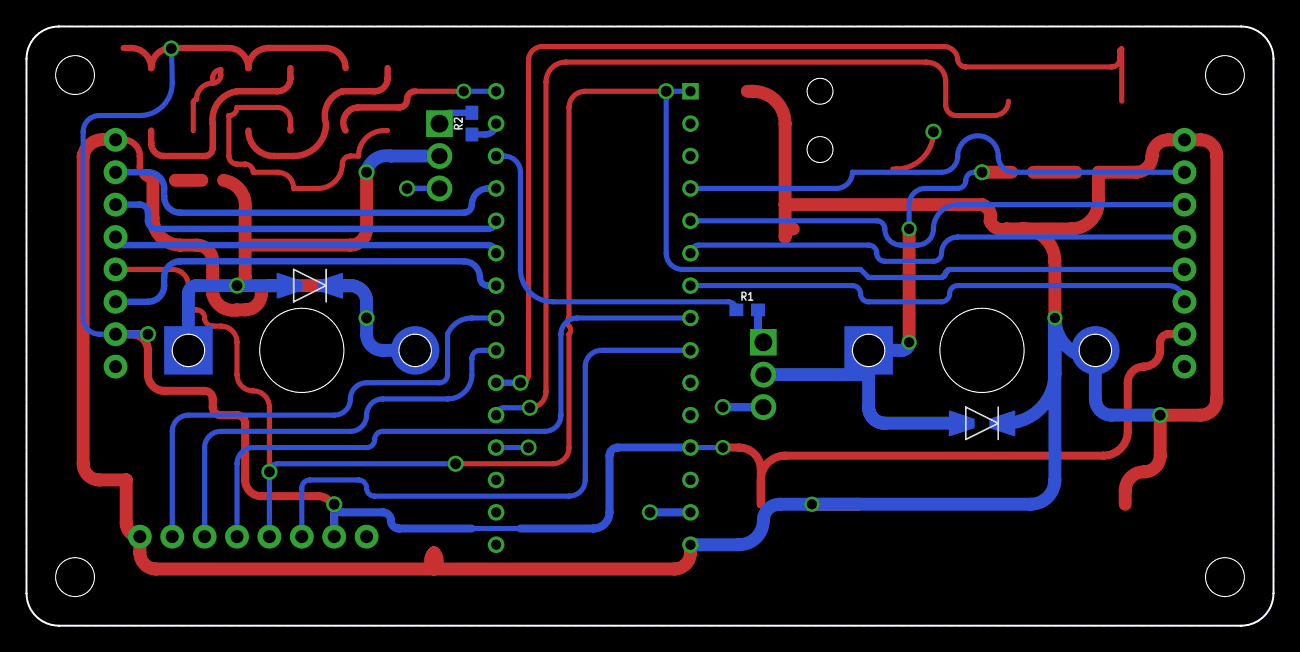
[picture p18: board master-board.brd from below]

Board: 2 copper layers, 97.8 x 47.0 mm, 31 parts (4 on the bottom side), 29 nets.

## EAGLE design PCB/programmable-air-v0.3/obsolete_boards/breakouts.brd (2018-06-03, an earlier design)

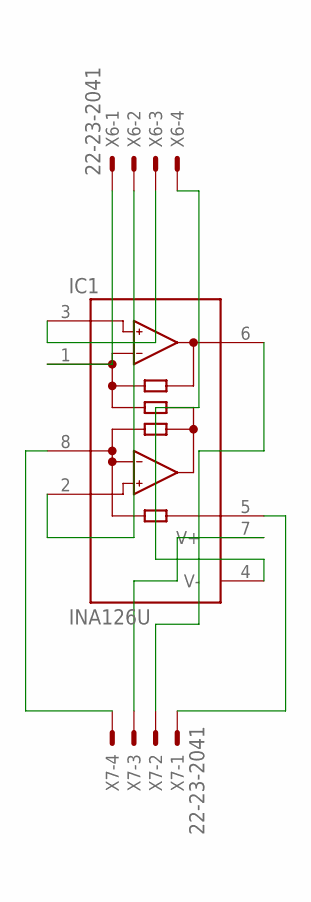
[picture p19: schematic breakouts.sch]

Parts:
IC1: INA126U; SO08
X6, X7: 22-23-2041

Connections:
unnamed: IC1.1 (RG), X6.1
unnamed: IC1.2 (-IN), X6.2
unnamed: IC1.3 (+IN), X6.3
unnamed: IC1.4 (V-), X6.4
unnamed: IC1.5 (REF), X7.1
unnamed: IC1.6 (OUT), X7.2
unnamed: IC1.7 (V+), X7.3
unnamed: IC1.8 (RG), X7.4

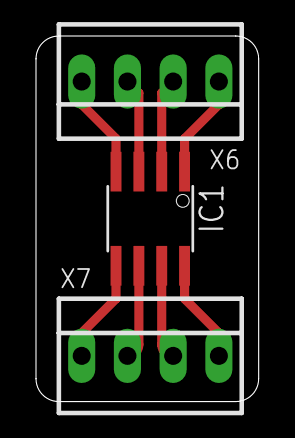
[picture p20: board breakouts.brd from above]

Board: 2 copper layers, 12.4 x 20.3 mm, 3 parts (0 on the bottom side), 8 nets.

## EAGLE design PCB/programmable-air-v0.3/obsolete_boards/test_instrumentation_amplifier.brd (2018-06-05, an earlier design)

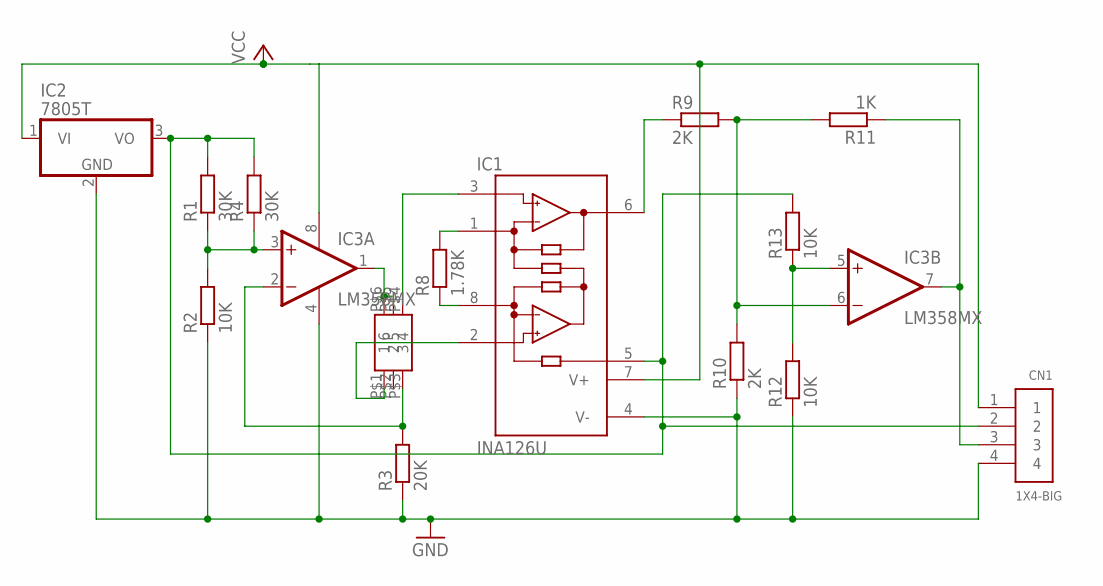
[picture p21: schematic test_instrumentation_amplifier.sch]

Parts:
CN1: 1X4-BIG; 1X04-BIG
IC1: INA126U; SO08
IC2: 7805T; TO220H
IC3: LM358MX; SO08
R1, R4: 30K; 0207/10
R2, R12, R13: 10K; 0207/10
R3: 20K; 0207/10
R8: 1.78K; 0207/10
R9, R10: 2K; 0207/10
R11: 1K; 0207/10
U$1: 2SMPP-03

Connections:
GND: CN1.4, IC1.4 (V-), IC2.2 (GND), IC3.4 (V-), R2.1, R3.1, R10.1, R12.1
unnamed: IC3.6 (-IN), R9.2, R10.2, R11.2
unnamed: IC1.8 (RG), R8.1
unnamed: IC1.3 (+IN), U$1.P$4 (4)
unnamed: CN1.2, IC1.5 (REF), IC2.3 (VO), R1.2, R4.2, R13.2
unnamed: IC1.1 (RG), R8.2
unnamed: IC1.2 (-IN), U$1.P$1 (1)
unnamed: IC3.1 (OUT), U$1.P$5 (5), U$1.P$6 (6)
unnamed: IC1.6 (OUT), R9.1
unnamed: IC3.3 (+IN), R1.1, R2.2, R4.1
unnamed: IC3.5 (+IN), R12.2, R13.1
unnamed: CN1.3, IC3.7 (OUT), R11.1
unnamed: IC3.2 (-IN), R3.2, U$1.P$3 (3)
VCC: CN1.1, IC1.7 (V+), IC2.1 (VI), IC3.8 (V+)

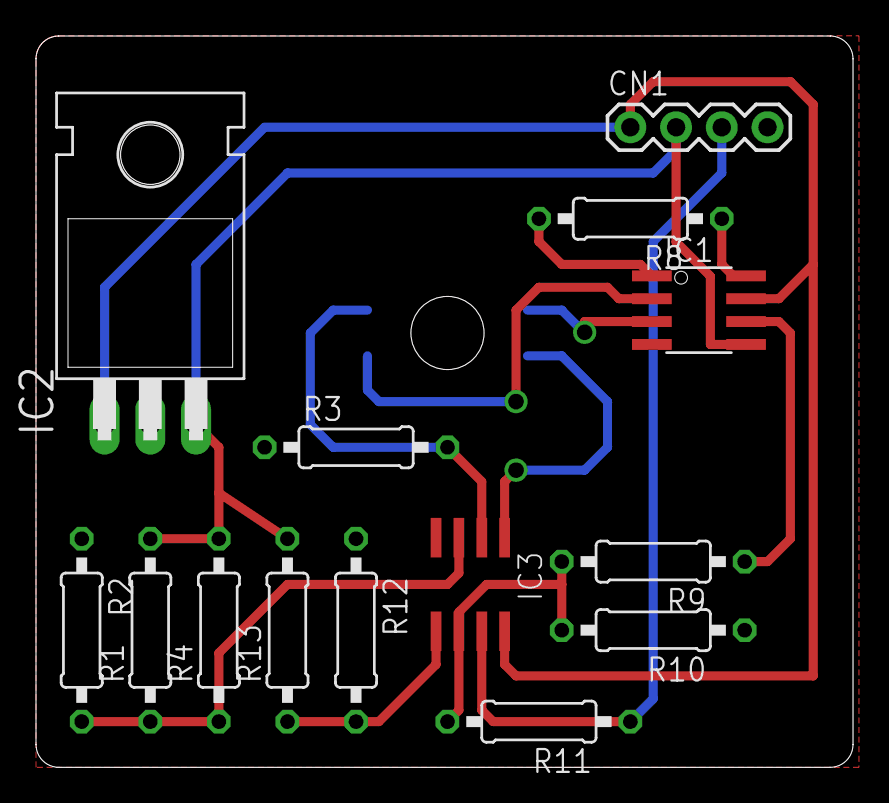
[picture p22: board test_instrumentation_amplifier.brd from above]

Board: 2 copper layers, 45.4 x 40.6 mm, 15 parts (0 on the bottom side), 14 nets.

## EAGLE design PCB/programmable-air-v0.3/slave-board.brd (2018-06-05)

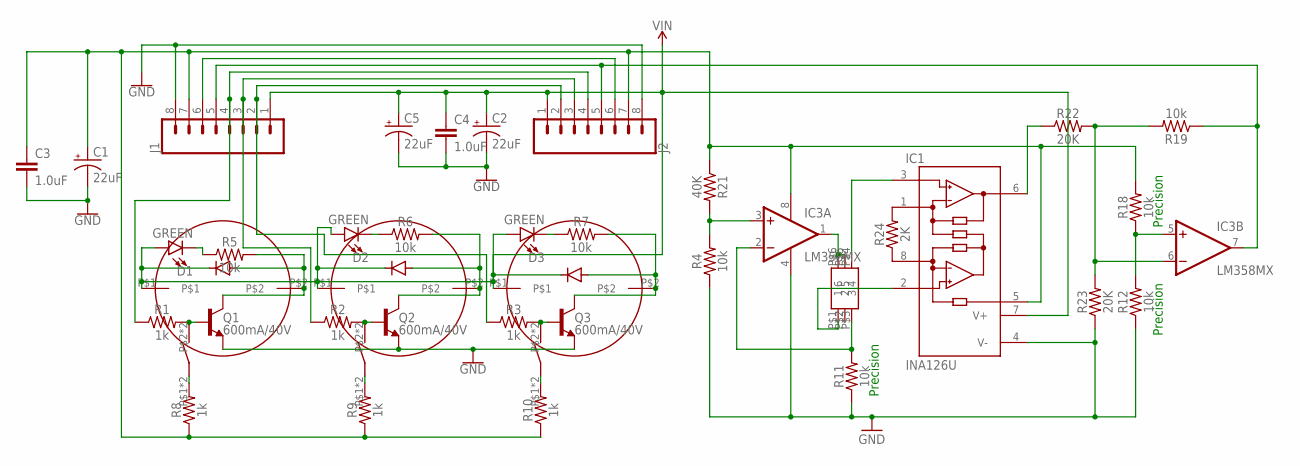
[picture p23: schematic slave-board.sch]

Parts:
C1, C2, C5: 22uF; PANASONIC_C
C3, C4: 1.0uF; 0603
D1, D2, D3: GREEN; LED-0603
IC1: INA126U; SO08
IC3: LM358MX; SO08
J1, J2: CONN_08"; 1X08
Q1, Q2, Q3: 600mA/40V; SOT23-3
R1, R2, R3, R8, R9, R10: 1k; 0603
R4, R5, R6, R7, R11, R12, R18, R19: 10k; 0603
R21: 40K; 0603
R22, R23: 20K; 0603
R24: 2K; 0603
U$1: 2SMPP-03
U$2, U$3, U$4: CJV23-SOLENOID-VALVE; CJV23
U$5, U$6, U$7: IN4148
U$8, U$9, U$10: BUTTON

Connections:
GND: C1.-, C2.-, C3.2, C4.2, C5.-, IC1.4 (V-), IC3.4 (V-), J1.8, J2.8, Q1.2 (E), Q2.2 (E), Q3.2 (E), R4.1, R11.1, R12.1, R23.1
unnamed: Q1.1 (B), R1.2, U$8.P$2, U$8.P$4
unnamed: Q2.1 (B), R2.2, U$9.P$2, U$9.P$4
unnamed: Q3.1 (B), R3.2, U$10.P$2, U$10.P$4
unnamed: IC1.2 (-IN), U$1.P$1 (1)
unnamed: J1.2, J2.2, R3.1
unnamed: D3.C, R7.1
unnamed: Q3.3 (C), R7.2, U$4.P$2, U$7.P$2
unnamed: Q2.3 (C), R6.2, U$3.P$2, U$6.P$2
unnamed: Q1.3 (C), R5.2, U$2.P$2, U$5.P$2
unnamed: J1.3, J2.3, R2.1
unnamed: D2.C, R6.1
unnamed: J1.4, J2.4, R1.1
unnamed: IC3.7 (OUT), J1.5, J2.5, R19.1
unnamed: J1.6, J2.6
unnamed: IC1.6 (OUT), R22.1
unnamed: C2.+, C4.1, C5.+, D1.A, D2.A, D3.A, IC1.7 (V+), J1.1, J2.1, U$2.P$1, U$3.P$1, U$4.P$1, U$5.P$1, U$6.P$1, U$7.P$1
unnamed: D1.C, R5.1
unnamed: IC3.1 (OUT), U$1.P$5 (5), U$1.P$6 (6)
unnamed: IC1.3 (+IN), U$1.P$4 (4)
unnamed: R8.2, U$8.P$1, U$8.P$3
unnamed: R9.2, U$9.P$1, U$9.P$3
unnamed: R10.2, U$10.P$1, U$10.P$3
unnamed: IC3.3 (+IN), R4.2, R21.2
unnamed: IC1.8 (RG), R24.1
unnamed: IC1.1 (RG), R24.2
unnamed: IC3.6 (-IN), R19.2, R22.2, R23.2
unnamed: C1.+, C3.1, IC1.5 (REF), IC3.8 (V+), J1.7, J2.7, R8.1, R9.1, R10.1, R18.2, R21.1
unnamed: IC3.5 (+IN), R12.2, R18.1
unnamed: IC3.2 (-IN), R11.2, U$1.P$3 (3)

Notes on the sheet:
Precision

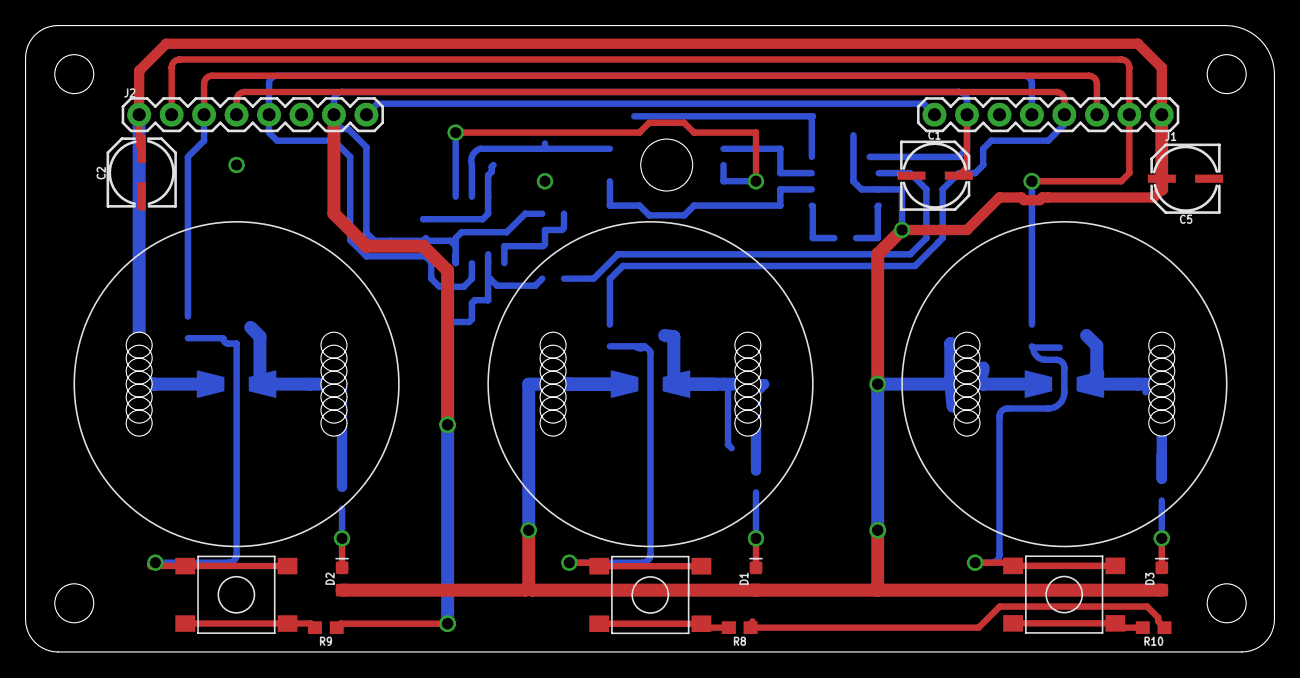
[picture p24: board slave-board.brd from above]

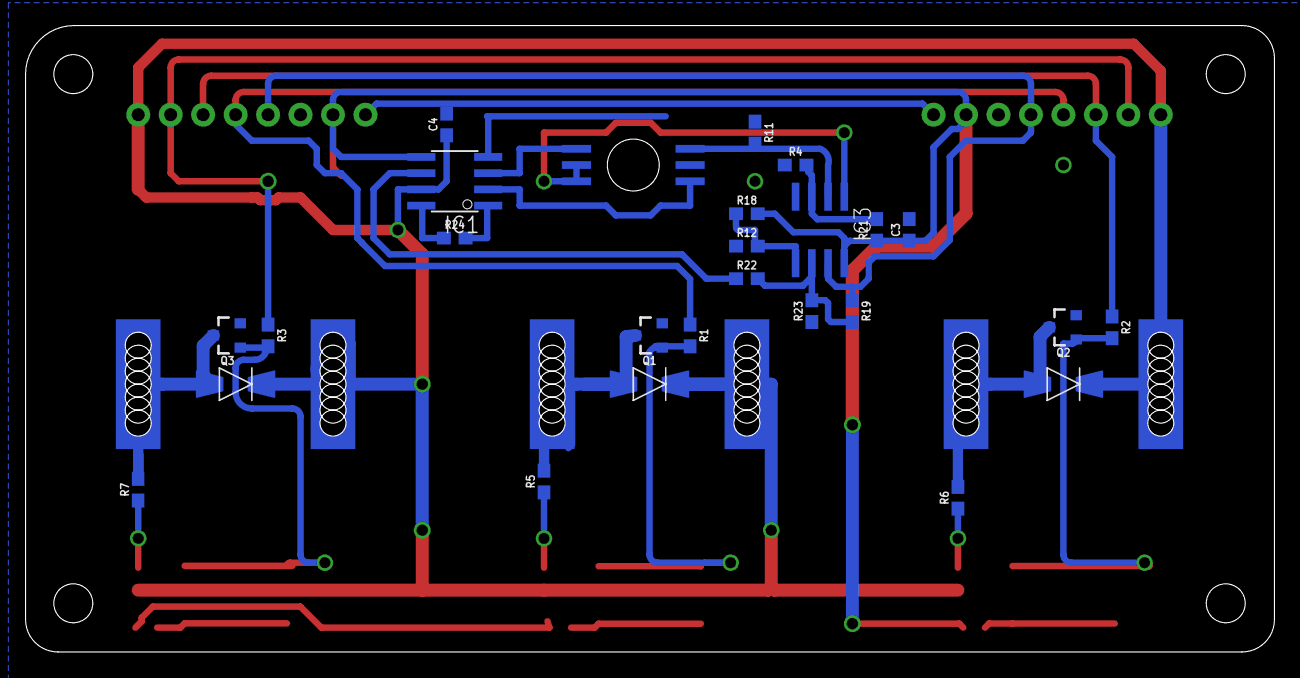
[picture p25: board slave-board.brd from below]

Board: 2 copper layers, 97.7 x 49.0 mm, 43 parts (25 on the bottom side), 30 nets.

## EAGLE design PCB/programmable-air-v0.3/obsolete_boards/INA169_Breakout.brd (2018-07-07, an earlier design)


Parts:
C1: 0.1uF; 0603-CAP
FRAME1: FRAME-LETTER; CREATIVE_COMMONS
JP1, JP2, JP5, JP6, JP7: M01PTH; 1X01
LOGO1: SFE_LOGO_NAME_FLAME.1_INCH; SFE_LOGO_NAME_FLAME_.1
LOGO2: OSHW-LOGOS; OSHW-LOGO-S
LOGO3: LOGO-SFESK; SFE-LOGO-FLAME
R1: 10; 1206
R2: 10k; 0603-RES
R3: RESISTORPTH-2W; AXIAL-0.8
R4: RESISTORPTH-1/4W; AXIAL-0.4
STANDOFF1, STANDOFF2, STANDOFF3, STANDOFF4: STAND-OFF
U1: INA169; SOT23-5

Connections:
GND: C1.1, JP6.1, R2.1, R4.P$1 (1), U1.2 (GND)
VCC: C1.2, JP5.1, U1.5 (V+)
VIN+: JP1.1, R1.1, R3.P$1 (1), U1.3 (VIN+)
VIN-: JP2.1, R1.2, R3.P$2 (2), U1.4 (VIN-)
VOUT: JP7.1, R2.2, R4.P$2 (2), U1.1 (OUT)

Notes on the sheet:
Shawn Hymel
For VCC = 5V
Range
Current Sense
10Ω
0.1Ω
3.5mA - 35mA
35mA - 350mA
350mA - 3.5A
Voltage Limits
VCC
Common Mode
(Vin+, Vin-)
-0.3V to 75V
VOUT = IS x RS x RL / 1kΩ


Board: 2 copper layers, 25.4 x 25.4 mm, 19 parts (1 on the bottom side), 5 nets.

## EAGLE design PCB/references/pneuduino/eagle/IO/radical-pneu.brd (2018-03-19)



Board: 2 copper layers, 30.5 x 50.8 mm, 28 parts (14 on the bottom side), 23 nets.

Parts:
C1, C2, C8, C10: 0.1uF; 0603-CAP
C3: 22uF; SMC_B
C5: 0.1uF; 0805
IC3: ATMEGA328; TQFP32-08
JP2, JP3: 1X04
PWR: CHIPLED_0603
Q1: 16Mhz; RESONATOR-SMD
R1, R2, R3: 10K; 0805
R5, R6: 4.7k; 0805
R9, R11, R12, R13: 1k; 0805
S1: TAC_SWITCHSMD; TACTILE-SWITCH-SMD
U2: NCP1117-5; LINEAR_SOT223
U$1, U$3: RS-014R05; SWITCH-11MM
U$2: PRS11S
U$10: ISP_POGO; POGO_ISP
U$12: FTDI_POGO
U$21: LTST-C19FD1WT; LTST

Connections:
+5V: C2.1, C3.+, C8.1, C10.1, IC3.4, IC3.6, IC3.18, IC3.20, R1.1, R2.1, R3.1, R5.1, R6.2, R11.2, U2.2, U2.4, U$2.1, U$10.2, U$12.4, U$21.+
A0/POT: IC3.23, U$2.2
D2/BTN: IC3.32, R1.2, U$1.A, U$1.H
D3/BTN: IC3.1, R2.2, U$3.A, U$3.H
D4: IC3.2, R9.2
D10: IC3.14, R12.2
DTR: C5.2, U$12.1
GND: C1.2, C2.2, C3.-, C8.2, C10.2, IC3.3, IC3.5, IC3.21, JP2.1, JP3.1, PWR.C, Q1.2, S1.1, S1.2, U2.1, U$1.B, U$1.D, U$2.3, U$3.B, U$3.D, U$10.6, U$12.5, U$12.6
MISO: IC3.16, U$10.1
MOSI: IC3.15, U$10.4
unnamed: IC3.8, Q1.1
unnamed: IC3.7, Q1.3
unnamed: PWR.A, R11.1
unnamed: R9.1, U$21.R
unnamed: R12.1, U$21.G
unnamed: R13.1, U$21.B
RESET: C5.1, IC3.29, R3.2, S1.3, S1.4, U$10.5
RX: IC3.30, U$12.3
SCK: IC3.17, R13.2, U$10.3
SCL: IC3.28, JP2.3, JP3.3, R6.1
SDA: IC3.27, JP2.2, JP3.2, R5.2
TX: IC3.31, U$12.2
VIN: C1.1, JP2.4, JP3.4, U2.3

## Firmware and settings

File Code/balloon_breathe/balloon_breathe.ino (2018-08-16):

#include "programmable_air.h"

int state = UN_KNOWN;

void setup() {
  Serial.begin(115200);

  initializePins();

  switchOnPump(1, 50);
  switchOnPump(2, 50);
}

void loop() {
  float pressure = readPressure();
  Serial.println(pressure);
  if (!digitalRead(btn1)) {
    blow(0);
  }
  else {
    if (!digitalRead(btn2)) {
      suck(0);
    }
    else {
      switch (state) {
        case UN_KNOWN:
          if (pressure > 514) {
            suck();
            state = DECREASING;
          }
          else {
            blow();
            state = INCREASING;
          }
          break;

        case INCREASING:
          if (pressure > 520) {
            suck();
            state = DECREASING;
          } else {
            blow();
          }
          break;

        case DECREASING:
          if (pressure < 500) {
            blow();
            state = INCREASING;
          } else {
            suck();
          }
          break;
      }
    }
  }
  for (int i = 0; i < 20; i++) {
    pressure = readPressure();
    Serial.println(pressure);
    delay(200);
  }
}

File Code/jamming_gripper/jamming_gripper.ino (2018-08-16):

#include "programmable_air.h"

void setup() {
  Serial.begin(115200);

  initializePins();
  pinMode(A5, INPUT_PULLUP);
  switchOnPump(1);
  switchOnPump(2);
}

void loop() {
  if (!digitalRead(btn2) || !digitalRead(A5)) {
    suck(0);
  }
  else {
    vent(0);
  }
  Serial.println(readPressure());
  delay(100);
}

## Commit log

2018-03-19 Slides complete
    [control_board_v2_bom.xlsx, radical-master.brd, radical-master.sch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]
2018-03-26 Restructured folders
    [control_board_v2_bom.xlsx, radical-master.brd, radical-master.sch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]
2018-04-02 Minor README changes
    [funnel.stl]
2018-04-14 Started work on PCB v0.1
    [BOM.ods, programmable-air.kicad_pcb, programmable-air.sch]
2018-04-14 Rearranged folders. Added PCB eagle files.
    [BOM.ods, aiyima-pump.brd, programmable-air.kicad_pcb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]
2018-04-14 Made pump nad valve PCB library. PCB Mockup made. Added arduino nano footprint.
    [test-pump.brd, testBoard.brd, testBoard.sch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]
2018-04-14 master board v0.1 complete.
    [master-board.brd, master-board.sch]
2018-04-14 Started work on slave PCB. Made changes to master pcb after testing
    [master-board.brd, master-board.sch, slave-board.sch]
2018-04-15 PCB v0.11 master ready for production
    [master-board.brd, master-board.sch]
2018-04-15 Forgot to add 5V input to slave boards
    [master-board.brd, master-board.sch, slave-board.sch]
2018-04-15 Fixed errors found after production, assembly and testing
    [master-board.brd, master-board.sch, slave-board.brd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]
2018-04-15 Final tests done. Pump test functional. Workinf on slave board now.
    [master-board.brd, master-board.sch, slave-board.brd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]
2018-04-15 Slave PCB v0.1 complete
    [slave-board.brd, slave-board.sch]
2018-04-15 Modified slave PCB v0.1 based on production and assembly
    [slave-board.brd]
2018-04-15 asthetic changes to slave PCB
    [slave-board.brd]
2018-04-17 After SMPP03 first test
    SMPP03 not working with hx711. Have to test it separately first. Made a test board for it. Added some vias to slave board. Added HX711 test code
    [test2SMPP-03.brd, test2SMPP-03.sch]
2018-04-18 Tested CJV23 valves
    Made pick and place machine. Added IO board 1. Have to design IO board PCB next.
2018-04-18 Started IOBoard1 schematic
    [IOborad1.sch]
2018-04-19 Added universal jamming gripper CAD and video. Modified basic_pick_and_place code.
    [HX711Serial_test.ino, basic_pick_and_place.ino]
2018-04-23 Added balloon CAD and media
2018-04-26 Added vacuum+blow balloon CAD and code
2018-04-26 Modified slave board to have LM10CN
    [slave-board.brd, slave-board.sch]
2018-04-27 Added PCB for testing SMPP with LM10 and HX711. Added gitignore.
    [slave-board.brd, slave-board.sch, testPresssureSensor.brd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]
2018-04-27 Added clearance for easier production
    [testPresssureSensor.brd]
2018-04-28 Post Rube Goldberg. Working on PCB v0.2
    [IOborad1.sch, aiyima-pump.brd, master-board.brd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]
2018-04-28 Master PCB v0.2 schematic and positioning complee. Going to start routing
    [master-board.brd, master-board.sch]
2018-04-28 Master PCB v0.2 routing complete
    [master-board.brd, master-board.sch]
2018-04-28 PCB v0.2 slave board ready
    [master-board.brd, slave-board.brd, slave-board.sch]
2018-04-28 PCB v0.2 cosmetic changes
    [master-board.brd]
2018-04-28 Minor fixes to slave PCB after assembly. Started work on test code for PCB v0.2
    [master-board.brd, slave-board.brd, slave-board.sch]
2018-05-05 Added pressure control code
2018-05-18 Added test circuit schematic for new amplifier of pressure sensor
    [master-board.sch, test_instrumentation_amplifier.brd, test_instrumentation_amplifier.sch]
2018-06-03 Working towards instrumentation amplifier instead of HX711
    MCP6001 was a huge mistake. 6V Vin max. Modifying circuit to LM358.
    [breakouts.brd, breakouts.sch, test_instrumentation_amplifier.brd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]
2018-06-03 LM358 test board ready
    [test_instrumentation_amplifier.brd, test_instrumentation_amplifier.sch]
2018-06-05 LM358 slave board ready
    [slave-board.brd, slave-board.sch, test_instrumentation_amplifier.brd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]
2018-06-05 LM358 slave board final
    [slave-board.brd, slave-board.sch]
2018-06-05 Master board + Slave board in single PCB ready.
    [master-board plus slave.brd, master-board plus slave.sch, slave-board.brd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]
2018-06-19 Minor changes to the PCB
    [master-board plus slave.brd]
2018-07-07 Sent PCBs for fabrication
    [INA169_Breakout.brd, INA169_Breakout.sch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]
2018-08-16 Sent for second production run. New Logo.
    [INA169_Breakout.brd, INA169_Breakout.sch, control_board_v2_bom.xlsx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]
2018-08-16 Added 3d models
    [CJV23_v2.f3d, master-board plus slave.brd, motor_v3.step]
2018-08-17 Much ado about 3d modelling
    [CJV23 v3.step, motor v4.step]
2018-08-26 After sending to elecrow for manufacturing. v0.3 complete. New Logo
    [CJV23_v2.f3d, INA169_Breakout.brd, INA169_Breakout.sch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]

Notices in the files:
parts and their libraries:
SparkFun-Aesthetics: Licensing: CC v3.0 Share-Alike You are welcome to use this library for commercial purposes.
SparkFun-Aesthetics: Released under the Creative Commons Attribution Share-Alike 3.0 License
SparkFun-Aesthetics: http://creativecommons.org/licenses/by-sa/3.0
